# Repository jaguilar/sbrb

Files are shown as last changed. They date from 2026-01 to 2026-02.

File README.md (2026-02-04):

# SBRB -- Another Arduino-based Self-Balancing Robot

## Overview

Well, is it really Arduino based? A little bit, but it's a funky
hybrid of ESP-IDF and Arduino code. This bot can be controlled
using a BLE gamepad like the Steam Controller (BLE firmware).

## Features

- Remote controllable
- Self-balancing
- Telemetry and bluetooth-based tuning
- Battery monitoring (assumes 2S LiPo, see schematics for voltage divider
  requirements)

## Schematics

There is a sort-of-working KiCad schematic in the `kicad` directory.
This is not actually what I used: I soldered together a protoboard.
Also, the pin configuration on the proto board and in the code is
significantly altered from what is shown in the schematic.

## Building

The bot uses 3D printed parts from this [OnShape document](https://cad.onshape.com/documents/8def695b0fbd504a5c261cca/w/9027d04ea9ab3dbc2eeb5165/e/62757f7892dd92c4c3207e76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).

## BOM

In addition to the 3D printed parts, you need:

* 2x 693ZZ bearings
* 2x 500 RPM N20 motors with gearboxes (I used [these](https://www.aliexpress.us/item/3256807135186419.html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))
* 2x TT motor wheels
* 1x 50x70mm perfboard
* 1x MPU-6050 breakout board
* 1x ESP32-S3 Zero Dev board
* 1x Mini360 buck converter
* 1x 20k resistor (buy a 0508 assortment of SMD parts, should have the caps and diode too)
* 1x 10k resistor
* 2x 100nF capacitor SMD 
* 1x 470uF capacitor throughhole (buy an assortment)
* 1x 100uF capacitor throughhole
* 1x 1N5819 Schottky diode
* 1x 3A fuse (you can use less, 2A would be fine)
* 1x throughhole switch capable of supporting same amperage as your
  fuse, or a lesser amperage and a MOSFET capable of supporting that current
* 1x TB6612FNG motor driver breakout board
* 1x 2S LiPo battery
* 3x JST-XH 2 pin through hole header
* 2x JST-XH 4 pin through hole header
* JST-XH female connectors for wires
* Various M2 and M3 hex head screws and nuts
* Various 24 AWG hookup wire
* XT30 connectors for battery

## Media



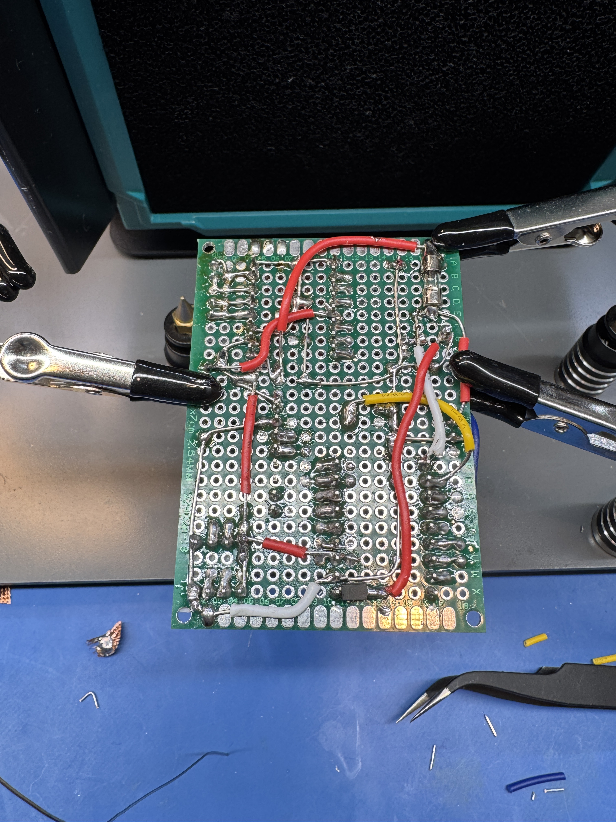
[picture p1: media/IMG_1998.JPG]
Perfboard picture 1


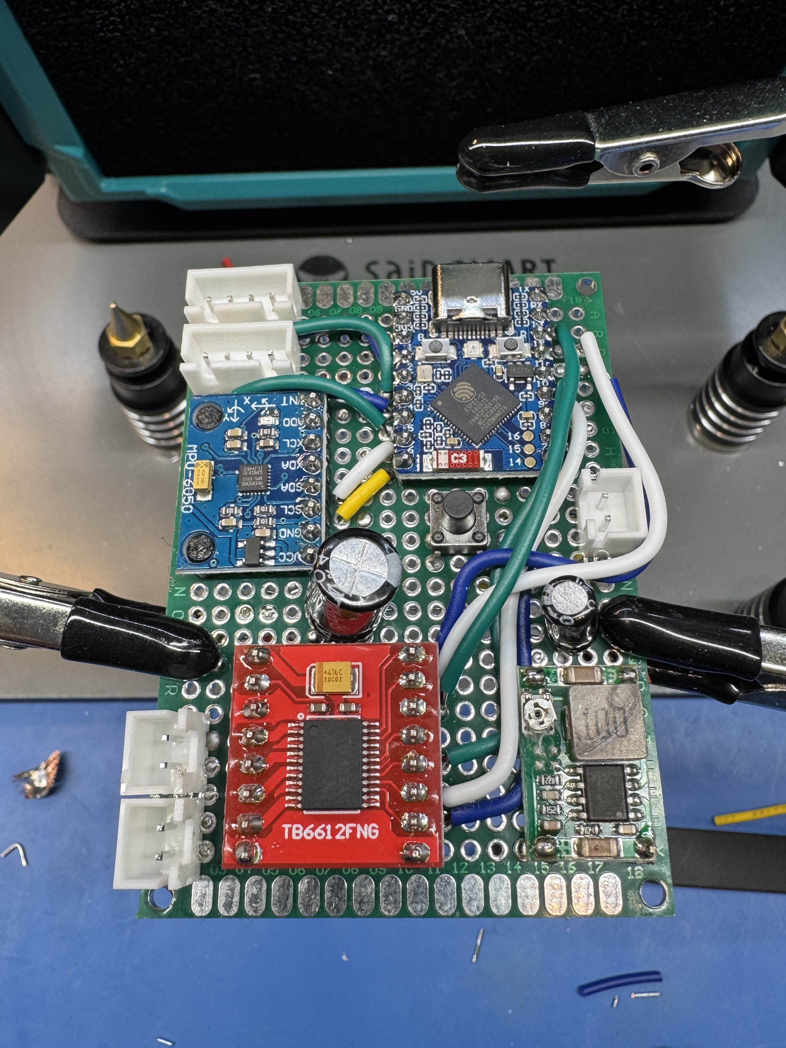
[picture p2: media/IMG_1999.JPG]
Perfboard picture 2


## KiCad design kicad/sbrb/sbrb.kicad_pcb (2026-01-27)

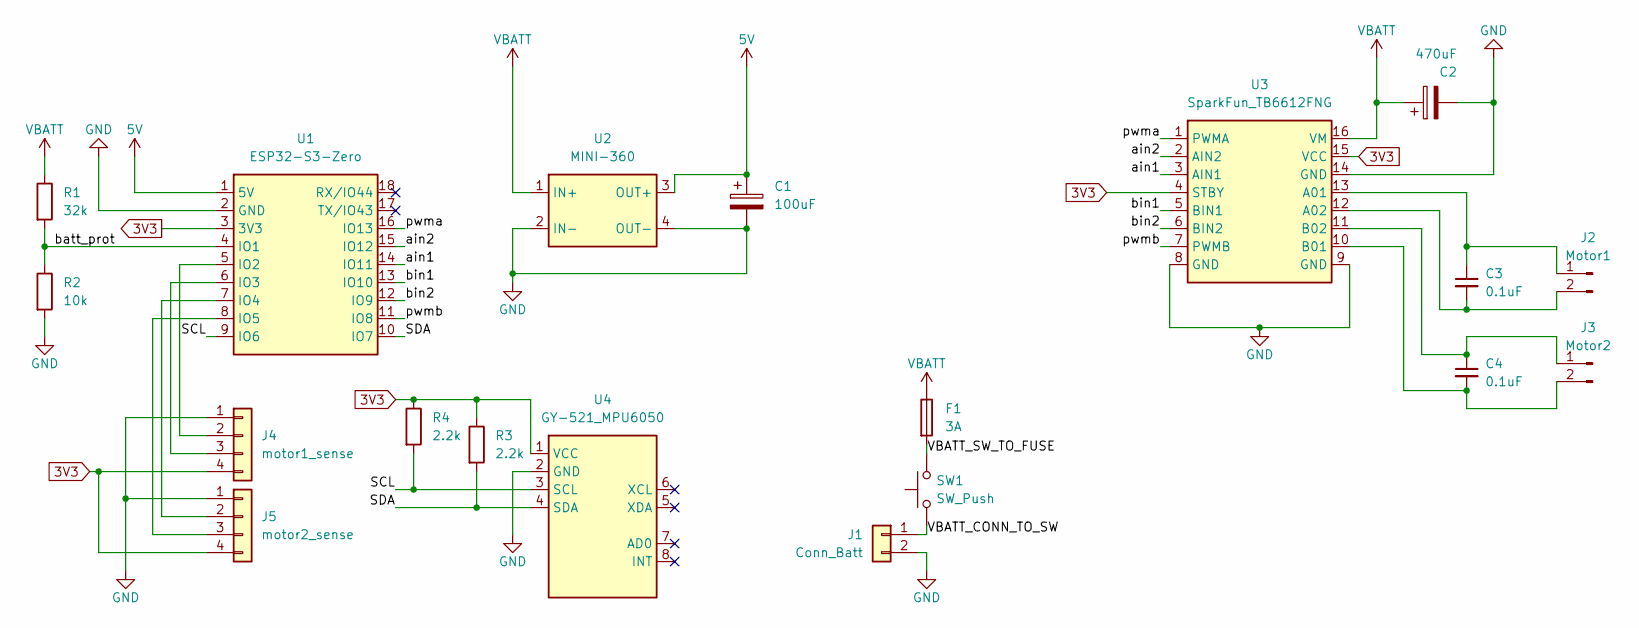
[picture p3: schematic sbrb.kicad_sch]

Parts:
C1: 100uF; CP_Radial_D6.3mm_P2.50mm
C2: 470uF; CP_Radial_D8.0mm_P3.80mm
C3, C4: 0.1uF; C_0805_2012Metric
F1: 3A; Fuse_Schurter_UMT250
J1: Conn_Batt; JST_XH_B2B-XH-AM_1x02_P2.50mm_Vertical
J2: Motor1; JST_XH_B2B-XH-AM_1x02_P2.50mm_Vertical
J3: Motor2; JST_XH_B2B-XH-AM_1x02_P2.50mm_Vertical
J4: motor1_sense; JST_XH_B4B-XH-AM_1x04_P2.50mm_Vertical
J5: motor2_sense; JST_XH_B4B-XH-AM_1x04_P2.50mm_Vertical
R1: 32k; R_0805_2012Metric
R2: 10k; R_0805_2012Metric
R3, R4: 2.2k; R_0805_2012Metric
SW1: SW_Push; SW_SPST_FSMSM
U1: ESP32-S3-Zero; ESP32-S3-Zero_Breakout
U2: MINI-360; mini360
U3: SparkFun_TB6612FNG; TB6612FNG_Breakout
U4: GY-521_MPU6050; GY-521

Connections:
3V3: J4.4, J5.4, R3.1, R4.1, U1.3 (3V3), U3.4 (STBY), U3.15 (VCC), U4.1 (VCC)
5V: C1.1, U1.1 (5V), U2.3 (OUT+)
/SCL: R4.2, U1.9 (IO6), U4.3 (SCL)
/SDA: R3.2, U1.10 (IO7), U4.4 (SDA)
/VBATT_CONN_TO_SW: J1.1, SW1.1
/VBATT_SW_TO_FUSE: F1.2, SW1.2
/ain1: U1.14 (IO11), U3.3 (AIN1)
/ain2: U1.15 (IO12), U3.2 (AIN2)
/batt_prot: R1.2, R2.1, U1.4 (IO1)
/bin1: U1.13 (IO10), U3.5 (BIN1)
/bin2: U1.12 (IO9), U3.6 (BIN2)
/pwma: U1.16 (IO13), U3.1 (PWMA)
/pwmb: U1.11 (IO8), U3.7 (PWMB)
GND: C1.2, C2.2, J1.2, J4.1, J5.1, R2.2, U1.2 (GND), U2.2 (IN-), U2.4 (OUT-), U3.8 (GND), U3.9 (GND), U3.14 (GND), U4.2 (GND)
unnamed: C3.1, J2.1, U3.13 (A01)
unnamed: C3.2, J2.2, U3.12 (A02)
unnamed: C4.1, J3.1, U3.11 (B02)
unnamed: C4.2, J3.2, U3.10 (B01)
unnamed: J4.2, U1.5 (IO2)
unnamed: J4.3, U1.6 (IO3)
unnamed: J5.2, U1.7 (IO4)
unnamed: J5.3, U1.8 (IO5)
VBATT: C2.1, F1.1, R1.1, U2.1 (IN+), U3.16 (VM)

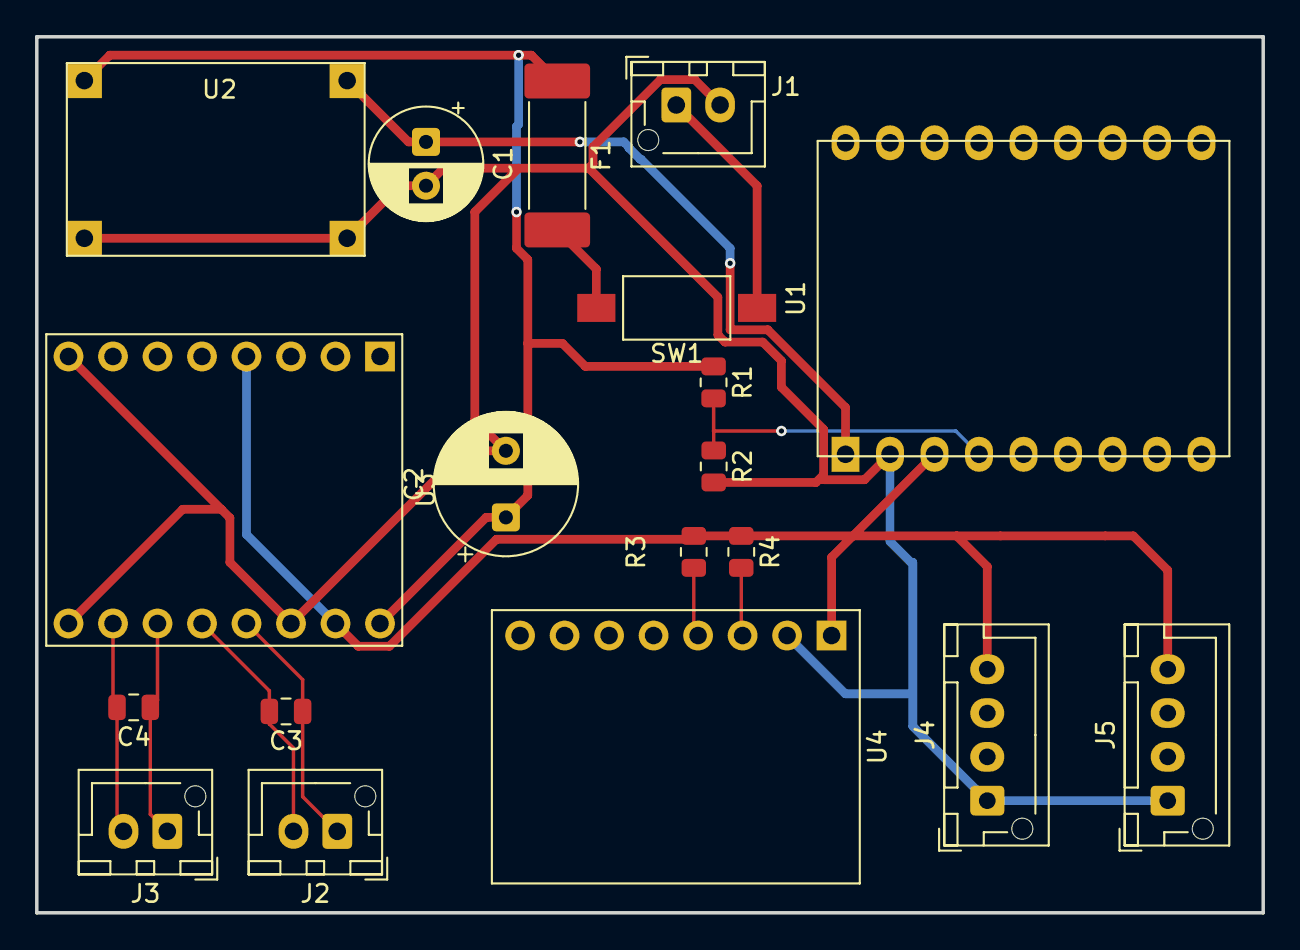
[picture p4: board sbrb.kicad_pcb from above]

Board: 4 copper layers, 70.0 x 50.0 mm, 19 parts (0 on the bottom side), 23 nets.

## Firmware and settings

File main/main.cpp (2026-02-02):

#include <Arduino.h>
#include <ESPmDNS.h>
#include <freertos/FreeRTOS.h>
#include <freertos/task.h>
#include <stdio.h>
#include <sys/unistd.h>

#include <cmath>
#include <cstdint>
#include <cstdio>
#include <cstdlib>
#include <cstring>
#include <functional>
#include <limits>
#include <memory>
#include <string_view>

#include "Adafruit_NeoPixel.h"
#include "FreeRTOSConfig.h"
#include "IPAddress.h"
#include "MPU6050.h"
#include "PIDController.h"
#include "ServoMotor.h"
#include "WiFi.h"
#include "WiFiUdp.h"
#include "Wire.h"
#include "driver/gpio.h"
#include "driver/rtc_io.h"
#include "esp32-hal-adc.h"
#include "esp32-hal-gpio.h"
#include "esp32-hal-log.h"
#include "esp32-hal.h"
#include "esp_err.h"
#include "esp_log.h"
#include "esp_sleep.h"
#include "esp_timer.h"
#include "freertos/idf_additions.h"
#include "freertos/task.h"
#include "pins_arduino.h"
#include "portmacro.h"
#include "soc/gpio_num.h"
#include "uni_property.h"

#ifdef CONFIG_BT_MODE_TUNE
#include <charconv>
#include <format>
#include <string>
#include <system_error>

#include "NimBLEAdvertising.h"
#include "NimBLEAttValue.h"
#include "NimBLEDevice.h"
#endif
#ifdef CONFIG_BT_MODE_PAD
#include <btstack_port_esp32.h>
#include <btstack_run_loop.h>
#include <gap.h>
#include <uni.h>
#endif

#define TAG "SBRB"

namespace sbrb {

constexpr int kMPU6050SDA = 5;
constexpr int kMPU6050SCL = 6;
constexpr int kBattVoltagePin = 7;
constexpr int kSleepPin = 8;

constexpr int kMotorLPwmPin = 12;
constexpr int kMotorLFwdPin = RX;
constexpr int kMotorLRevPin = 13;
constexpr int kMotorLPulsePin = 2;
constexpr int kMotorLControlPin = 1;

constexpr int kMotorRPwmPin = 9;
constexpr int kMotorRFwdPin = 11;
constexpr int kMotorRRevPin = 10;
constexpr int kMotorRPulsePin = 3;
constexpr int kMotorRControlPin = 4;

constexpr int kNeoPixelPin = 21;
constexpr int kNeoPixelCount = 1;
static Adafruit_NeoPixel neo_pixel(kNeoPixelCount, kNeoPixelPin,
                                   NEO_RGB + NEO_KHZ800);

constexpr float kBattVoltageScale = 3.3f;
constexpr float kDividerRatio = 1.0f / 3.0f;

std::unique_ptr<ServoMotor> motor_l;
std::unique_ptr<ServoMotor> motor_r;
std::unique_ptr<MPU6050> mpu;

struct State {
  int64_t now = millis();
  int loop_iter = 0;

  int last_steering_iter = 0;
  uint32_t now_us = micros();
  float dt = 0;  // The change in time (s) since the last sample.

  float pitch = -90;  // Degrees, negative if we're tilted forward.
  float pitch_rate =
      0;  // Rate in the change of pitch (i.e. the raw gyro reading.)

  float yaw_rate = 0;     // Degrees/s, smoothed via EWMA.
  float wheel_speed = 0;  // Degrees/s, averaged between the two motors,
                          // smoothed via EWMA.
  float accel = 0;        // Degrees/s^2, smoothed via EWMA.

  float wheel_speed_left = 0;
  float wheel_speed_right = 0;

  int64_t last_time_standing = now - 1000;
  bool fallen() const { return now - last_time_standing > 250; }

  // Command state, useful for debugging.
  float commanded_yaw_rate;
  float commanded_speed;
  float commanded_pitch;
  float commanded_duty_left;
  float commanded_duty_right;

  // The "now_us" time of the sample that was last used to compute the balance
  // and steering commands. Used to compute dt for the PID controller update
  // loops.
  uint32_t last_balance_cmd_us = 0;
  uint32_t last_steering_cmd_us = 0;
};

// The controller for the robot. Contains the PID controllers for the robot.
struct Controller {
  // The pitch controller takes in the current pitch and the desired pitch and
  // emits motor average duty cycle to achieve that pitch. Basic tuning
  // intuition is if we're pitched forward of where we want to be, we should be
  // running the motors *toward* the direction we're pitched. Running the motors
  // in one direction tends to push the wheels in the opposite direction,
  // gain will be positive.
  PIDController pitch_controller{PIDController::Params{
      .kp = 30.f,
      .ti = 0.6f,
      .td = 0.035f,
      .output_range = {{-255, 255}},
  }};

  // Controls the speed of the wheels by adjusting the target pitch angle.
  // The gain on this controller is quite low, because the wheel speed is in
  // degrees per second. The idea here is that the desired pitch might be
  // only a couple of degrees forward when we want to go 720 degrees per second.
  //
  // The gain's sign is set this way: if we want to go forward, we need to pitch
  // forward. To pitch forward, we need to the pitch to be negative.
  PIDController wheel_speed_controller{{
      .kp = -0.005f,
      .ti = 2.5f,
      .td = 0.01f,
      .output_range = {{-20, 20}},
  }};

  // Controls the differential drive that controls the yaw rate. (I.e. for each
  // degree per second of yaw rate error, how much duty cycle should we add to
  // the left motor and subtract from the right motor?)
  //
  // As a reminder to myself, in robotics, clockwise rotation about Z is
  // negative. Error is setpoint - measurement. So, let's suppose setpoint is
  // zero, and I observe that I'm turning to the right (measurement is
  // negative). That will make my error positive. When my error is positive, I
  // need to turn left to compensate, which is to say that I need to add duty to
  // the right motor and subtract from the left. So the output of this is the
  // differential duty cycle to add to the right motor and subtract from the
  // left.
  PIDController yaw_rate_controller{PIDController::Params{
      .kp = 0.25f, .ti = 0.0, .td = 0.0f, .output_range = {{-50, 50}}}};

  int32_t axis_y = 0;  // Used to compute setpoints.
  int32_t axis_rx = 0;
};
Controller pid_controllers;

static volatile bool sleep_soon = false;
void IRAM_ATTR SleepPinISR() { sleep_soon = true; }

[[noreturn]] void GoToSleep() {
  motor_l->DeepSleepPrepare();
  motor_r->DeepSleepPrepare();

  neo_pixel.clear();
  neo_pixel.show();

  const auto pin = static_cast<gpio_num_t>(kSleepPin);
  pinMode(pin, INPUT_PULLUP);
  do {
    delay(100);  // Debounce, the sleep button.
  } while (!digitalRead(pin));
  delay(25);

  // We need to respect all holds, particularly on the motor pins,
  // while we are asleep.
  gpio_deep_sleep_hold_en();

  rtc_gpio_init(pin);
  rtc_gpio_pullup_en(pin);
  esp_sleep_enable_ext0_wakeup(pin, 0);
  esp_deep_sleep_start();
}

void WakeUp() {
  rtc_gpio_deinit(static_cast<gpio_num_t>(kSleepPin));
  motor_l->DeepSleepResume();
  motor_r->DeepSleepResume();

  // Don't finish waking up until the sleep button is released.
  pinMode(kSleepPin, INPUT_PULLUP);
  while (!digitalRead(kSleepPin)) {
    delay(100);
  }
  delay(50);
}

static void InitTuningService();

// The battery is connected to kBattVoltagePin via a voltage divider.
// The divider is 20k/10k. This means we'll see a voltage which is roughly
// 2/3rds of the actual battery voltage.
int BatteryMillivolts() {
  constexpr int kMillivoltsScale = 16 / kDividerRatio;
  const int batt_milivolts =
      (analogReadMilliVolts(kBattVoltagePin) * kMillivoltsScale) / 16;
  return batt_milivolts;
}

static int smoothed_battery_millivolts = -1000;
void MonitorBattery(void*) {
  constexpr float kAlpha = 0.05;
  if (smoothed_battery_millivolts < -100) {
    smoothed_battery_millivolts = BatteryMillivolts();
  } else {
    smoothed_battery_millivolts = (smoothed_battery_millivolts * (1 - kAlpha) +
                                   BatteryMillivolts() * kAlpha);
  }
}

#if CONFIG_TELEMETRY_ENABLED
struct TelemetryData {
  uint32_t now_ms;
  float yaw_rate;
  float yaw_p;
  float yaw_i;
  float yaw_d;
  float yaw_err;
  float yaw_cmd;
  float motor_l_duty;
  float motor_r_duty;
  float pitch;
};

static portMUX_TYPE telemetry_state_mu = portMUX_INITIALIZER_UNLOCKED;
static TelemetryData telemetry_state;
static IPAddress telemetry_addr;
static constexpr int kTeleplotPort = 47269;
static WiFiUDP udp;

void QueueTelemetry(const TelemetryData& d) {
  if (portTRY_ENTER_CRITICAL(&telemetry_state_mu, 0)) {
    telemetry_state = d;
    portEXIT_CRITICAL(&telemetry_state_mu);
  }
}

void SendTelemetry(void*) {
  static uint32_t last_send = 0;
  if (!portTRY_ENTER_CRITICAL(&telemetry_state_mu, 0)) {
    ESP_LOGW("SBRB", "Failed to enter critical section for telemetry");
    return;
  }
  TelemetryData state = telemetry_state;
  IPAddress addr = telemetry_addr;
  portEXIT_CRITICAL(&telemetry_state_mu);
  if (addr == IPAddress()) {
    ESP_LOGW("SBRB", "Telemetry address not resolved");
    return;
  }
  if (state.now_ms == last_send) {
    ESP_LOGW("SBRB", "Telemetry not updated");
    return;
  }
  last_send = state.now_ms;

  // Assemble a UDP packet containing the telemetry. For the sake of argument we
  // will assume no more than one packet is needed, but this is a hack.
  char packet_buf[1432];
  int packet_len = 0;

  auto add_field = [&](std::string_view name, float value) {
    int written = snprintf(&packet_buf[packet_len],
                           sizeof(packet_buf) - packet_len, "%*s:%lu:%.4f\n",
                           name.size(), name.data(), state.now_ms, value);
    if (written < 0 || written >= sizeof(packet_buf) - packet_len) {
      packet_buf[packet_len] = 0;
    }
    packet_len += written;
  };

  add_field("dyaw", state.yaw_rate);
  add_field("yaw_p", state.yaw_p);
  add_field("yaw_i", state.yaw_i);
  add_field("yaw_d", state.yaw_d);
  add_field("yaw_err", state.yaw_err);
  add_field("yaw_cmd", state.yaw_cmd);
  add_field("motor_l_duty", state.motor_l_duty);
  add_field("motor_r_duty", state.motor_r_duty);
  add_field("pitch", state.pitch);

  udp.beginPacket(addr, kTeleplotPort);
  udp.write(reinterpret_cast<const uint8_t*>(packet_buf), packet_len);
  if (udp.endPacket() < 0) {
    ESP_LOGD("SBRB", "Failed to send telemetry packet of length %d",
             packet_len);
  } else {
    ESP_LOGD("SBRB", "Sent telemetry packet of length %d", packet_len);
  }
}

TelemetryData MakeTelemetryPacket(const State& state,
                                  const Controller& controller) {
  TelemetryData packet;
  packet.now_ms = state.now;
  packet.yaw_rate = state.yaw_rate;
  packet.yaw_p = controller.yaw_rate_controller.p();
  packet.yaw_i = controller.yaw_rate_controller.i();
  packet.yaw_d = controller.yaw_rate_controller.d();
  packet.yaw_err = controller.yaw_rate_controller.error();
  packet.yaw_cmd = state.commanded_yaw_rate;
  packet.motor_l_duty = state.commanded_duty_left;
  packet.motor_r_duty = state.commanded_duty_right;
  packet.pitch = state.pitch;
  return packet;
}

#endif

void LowPriorityTasks(void*) {
  struct {
    void (*work)(void*);
    uint32_t period;
    uint32_t last_done = millis() - period;
    bool IsExpired() const { return millis() - last_done > period; }
    void MarkDone() { last_done = millis(); }
    uint32_t SleepDuration() const {
      const uint32_t since_done = millis() - last_done;
      if (since_done > period) {
        return 0;
      }
      return period - since_done;
    }
  } jobs[] = {
      {.work = MonitorBattery, .period = 1000},
#if CONFIG_TELEMETRY_ENABLED
      {.work = SendTelemetry, .period = 50},
#endif
  };

  while (true) {
    uint32_t sleep_time = std::numeric_limits<uint32_t>::max();
    for (auto& job : jobs) {
      if (job.IsExpired()) {
        job.work(nullptr);
        job.MarkDone();
      }
      sleep_time = std::min(sleep_time, job.SleepDuration());
    }
    if (sleep_time > 50) {
      ESP_LOGW(TAG, "Sleep duration %d too long", sleep_time);
      sleep_time = 50;
    }
    vTaskDelay(pdMS_TO_TICKS(sleep_time));
  }
}

constexpr int kBalanceFreq = 500;
constexpr int kSteeringFreq = 20;
constexpr int kSteerOncePerIters = kBalanceFreq / kSteeringFreq;

void UpdateState(State& state, bool log_details = false) {
  state.now = millis();
  state.loop_iter++;
  auto now_us = micros();
  state.dt = (now_us - state.now_us) / 1000000.0f;
  state.now_us = now_us;

  if (state.dt < 0.0005f) {
    // Not enough time has passed since the last sample. Skip this iteration.
    return;
  }

  constexpr float kAlpha = 0.98f;
  constexpr float kRadToDeg = 180.0f / 3.14159265f;

  // MPU6050 Defaults
  constexpr float kAccelScale = 16384.0f;
  constexpr float kGyroScale = 32.8f;
  int16_t ax_raw, ay_raw, az_raw, gx_raw, gy_raw, gz_raw;
  mpu->getMotion6(&ax_raw, &ay_raw, &az_raw, &gx_raw, &gy_raw, &gz_raw);

  // Convert to physical units
  const float ax = ax_raw / kAccelScale;
  const float ay = ay_raw / kAccelScale;
  const float az = az_raw / kAccelScale;
  const float gy = gy_raw / kGyroScale;
  const float gz = gz_raw / kGyroScale;

  float acc_angle_y = atan2(-ax, sqrt(ay * ay + az * az)) * kRadToDeg;
  state.pitch =
      (state.pitch + gy * state.dt) * kAlpha + (1.0f - kAlpha) * acc_angle_y;

  // Update pitch and yaw rates. Tuned for a cutoff frequency of ~4Hz.
  constexpr auto kGyroAlpha = 0.05f;
  constexpr auto kGryoAlphaInv = 1.0f - kGyroAlpha;
  state.pitch_rate = kGyroAlpha * gy + kGryoAlphaInv * state.pitch_rate;
  state.yaw_rate = kGyroAlpha * gz + kGryoAlphaInv * state.yaw_rate;

  state.wheel_speed_left = motor_l->GetSpeed();
  state.wheel_speed_right = motor_r->GetSpeed();
  const float avg_speed =
      (state.wheel_speed_left + state.wheel_speed_right) / 2.0f;
  // Wheel speed is filtered less aggressively than the gyro since we expect
  // a higher frequency of real wheel speed changes.
  constexpr auto kSpeedAlpha = 0.1f;
  const float raw_accel = (avg_speed - state.wheel_speed) / state.dt;
  state.accel = kSpeedAlpha * raw_accel + (1.0f - kSpeedAlpha) * state.accel;
  state.wheel_speed =
      kSpeedAlpha * avg_speed + (1.0f - kSpeedAlpha) * state.wheel_speed;

  const float abspitch = std::abs(state.pitch);
  if (state.fallen() && abspitch <= 3) {
    state.last_time_standing = state.now;
  } else if (abspitch <= 30) {
    state.last_time_standing = state.now;
  }
}

void Control(State& state, Controller& control) {
  // Compute the setpoints for desired turn rate and forward and reverse.
  constexpr float kSpeedRange = 920.0f;  // 120 RPM is max commanded speed.
  constexpr float kYawRange =
      180.0f;  // 90 degrees per second is max turn rate.
  constexpr float kSpeedSaturation =
      512.0f;  // Once the y-axis reaches +-512, the output will be saturated.
  constexpr float kYawSaturation =
      450.0f;  // Once the rx-axis reaches +-450, the output will be saturated.

  // axis_y+ is backward, but speed+ is forward, so we negate the axis.
  const float speed_setpoint =
      std::clamp(-control.axis_y * kSpeedRange / kSpeedSaturation, -kSpeedRange,
                 kSpeedRange);
  // axis_rx+ is clockwise rotation, but yaw rate is negative for clockwise.
  const float yaw_setpoint = std::clamp(
      -control.axis_rx * kYawRange / kYawSaturation, -kYawRange, kYawRange);

  if (state.loop_iter - state.last_steering_iter >= kSteerOncePerIters) {
    state.last_steering_iter = state.loop_iter;
    // Try to find a pitch that will get us to the desired speed.
    const float dt = (state.now_us - state.last_steering_cmd_us) / 1000000.0f;
    state.commanded_pitch = control.wheel_speed_controller.Compute(
        speed_setpoint, state.wheel_speed, state.accel, dt);
    state.last_steering_cmd_us = state.now_us;
  }

  // Try to find a duty cycle that will get us to the desired pitch.
  const float dt = (state.now_us - state.last_balance_cmd_us) / 1000000.0f;
  float duty = control.pitch_controller.Compute(
      state.commanded_pitch, state.pitch, state.pitch_rate, dt);
  float yaw_duty =
      control.yaw_rate_controller.Compute(yaw_setpoint, state.yaw_rate, dt);
  state.last_balance_cmd_us = state.now_us;

  // Scale the duty cycle based on the battery voltage.
  // We did the initial robot tuning at 7V on a bench power supply.
  // If the battery voltage is higher than that we need to command
  // a lower duty cycle to compensate. This does also mean we'll never
  // run the motor at full power when the battery is fully charged,
  // but that's okay because doing it this way means we'll give a
  // consistent experience no matter the charge level. Note that there
  // is no need for clamping here as the robot will shut off if the
  // power is substantially lower than the tuning voltage to protect
  // the battery.
  constexpr float kTuningVbattMV = 7000;
  if (smoothed_battery_millivolts > 6000) {
    // Don't bother with this step if we're not connected to motor power.
    duty *= kTuningVbattMV / smoothed_battery_millivolts;
    yaw_duty *= kTuningVbattMV / smoothed_battery_millivolts;
  }

  state.commanded_duty_left = duty - yaw_duty;
  state.commanded_duty_right = duty + yaw_duty;
  motor_l->SetDuty(state.commanded_duty_left);
  motor_r->SetDuty(state.commanded_duty_right);
}

void SetPixelColor(float pitch) {
  constexpr float kRedPitch = 10.0f;

  const float lerp = std::min(1.0f, std::abs(pitch) / kRedPitch);
  neo_pixel.setPixelColor(0, lerp * 255, (1.0f - lerp) * 255, 0);
  neo_pixel.show();
}

#if CONFIG_BT_MODE_TUNE

char cmd_buf[100];
int cmd_idx = 0;

void DoTuningCommand(std::string_view cmd) {
  while (true) {
    // Strip leading whitespace
    while (!cmd.empty() && std::isspace(cmd.front())) {
      cmd.remove_prefix(1);
    }
    if (cmd.empty()) break;

    // Find the end of the command string (first whitespace)
    size_t cmd_end = 0;
    while (cmd_end < cmd.size() && !std::isspace(cmd[cmd_end])) {
      cmd_end++;
    }

    std::string_view command = cmd.substr(0, cmd_end);
    cmd.remove_prefix(cmd_end);

    // Strip whitespace before value
    while (!cmd.empty() && std::isspace(cmd.front())) {
      cmd.remove_prefix(1);
    }

    if (cmd.empty()) {
      log_e("Command %.*s missing value", static_cast<int>(command.size()),
            command.data());
      break;
    }

    float value;
    auto result = std::from_chars(cmd.data(), cmd.data() + cmd.size(), value);
    if (result.ec == std::errc()) {
      cmd.remove_prefix(result.ptr - cmd.data());

      if (command == "pp") {
        pid_controllers.pitch_controller.set_kp(value);
        ESP_LOGI(TAG, "Pitch: Set kp to %f", value);
      } else if (command == "pi") {
        pid_controllers.pitch_controller.set_ti(value);
        ESP_LOGI(TAG, "Pitch: Set ti to %f", value);
      } else if (command == "pd") {
        pid_controllers.pitch_controller.set_td(value);
        ESP_LOGI(TAG, "Pitch: Set td to %f", value);
      } else if (command == "wp") {
        pid_controllers.wheel_speed_controller.set_kp(value);
        ESP_LOGI(TAG, "Wheel: Set kp to %f", value);
      } else if (command == "wi") {
        pid_controllers.wheel_speed_controller.set_ti(value);
        ESP_LOGI(TAG, "Wheel: Set ti to %f", value);
      } else if (command == "wd") {
        pid_controllers.wheel_speed_controller.set_td(value);
        ESP_LOGI(TAG, "Wheel: Set td to %f", value);
      } else if (command == "db") {
        motor_l->set_deadband(static_cast<int>(value));
        motor_r->set_deadband(static_cast<int>(value));
        ESP_LOGI(TAG, "Set deadband to %d", static_cast<int>(value));
      } else {
        log_e("Unknown command: %.*s", static_cast<int>(command.size()),
              command.data());
      }
    } else {
      log_e("Failed to parse value for command %.*s",
            static_cast<int>(command.size()), command.data());
      // Consume the bad token
      while (!cmd.empty() && !std::isspace(cmd.front())) {
        cmd.remove_prefix(1);
      }
    }
  }
}

void MaybeReadCommand() {
  if (!Serial.available()) return;
  int c;
  while (cmd_idx < sizeof(cmd_buf) - 1 &&
         (cmd_idx == 0 || cmd_buf[cmd_idx - 1] != '\n') &&
         (c = Serial.read()) != -1) {
    cmd_buf[cmd_idx++] = c;
    ESP_LOGI(TAG, "Received char: %c", c);
  }

  std::string_view cmd_view(cmd_buf, cmd_idx);
  if (!cmd_view.empty() &&
      (cmd_view.back() == '\n' || cmd_view.back() == '\r')) {
    DoTuningCommand(cmd_view);
    std::memset(cmd_buf, 0, sizeof(cmd_buf));
    cmd_idx = 0;
  }
}
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
void loop() {
  using namespace sbrb;
  static State state;
  static int print_counter = 0;
  bool print_details = false;
  if (print_details) print_counter = 0;

  static auto last_loop_start = micros();
  const auto wait_start = micros();
  auto interloop_time = wait_start - last_loop_start;
  last_loop_start = wait_start;

  xTaskNotifyWait(0, 1, nullptr, portMAX_DELAY);
  const auto loop_start = micros();
  UpdateState(state, print_details);

  // Do shutdown checks first and foremost.
  if (smoothed_battery_millivolts < 6800 || sleep_soon) {
    // GoToSleep();
  }

  SetPixelColor(state.pitch);

  if (state.fallen()) {
    motor_l->SetDuty(0);
    motor_r->SetDuty(0);
    pid_controllers.pitch_controller.Reset();
    pid_controllers.wheel_speed_controller.Reset();
    pid_controllers.yaw_rate_controller.Reset();
  } else {
    Control(state, pid_controllers);
  }

#if CONFIG_TELEMETRY_ENABLED
  static int32_t last_telemetry = state.now;
  if (state.now - last_telemetry > 50) {
    last_telemetry = state.now;
    TelemetryData packet = MakeTelemetryPacket(state, pid_controllers);
    QueueTelemetry(packet);
  }
#endif

  const auto loop_end = micros();
  static int last_loop_log = millis();
  if (millis() - last_loop_log > 1000 && !print_details && print_counter != 0) {
    // Check for violated loop timing expectations.
    if (interloop_time > 2500) {
      ESP_LOGE(TAG, "Interloop time was %d usec",
               static_cast<int>(interloop_time));
    } else if (loop_end - loop_start > 1500) {
      ESP_LOGE(TAG, "Control loop took %d usec",
               static_cast<int>(loop_end - loop_start));
    } else {
      return;  // We didn't print anything.
    }
    last_loop_log = millis();
  }
}

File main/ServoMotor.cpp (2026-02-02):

#include "ServoMotor.h"

#include <Arduino.h>

#include <algorithm>
#include <cstdint>
#include <memory>
#include <utility>

#include "driver/gpio.h"
#include "driver/pulse_cnt.h"
#include "esp_check.h"
#include "esp_err.h"
#include "freertos/idf_additions.h"
#include "portmacro.h"
#include "freertos/semphr.h"
#include "soc/gpio_num.h"

// Define LOG_TAG if not already defined for ESP logging macros
#ifndef LOG_TAG
#define LOG_TAG "ServoMotor"
#endif

ServoMotor::ServoMotor(pcnt_unit_handle_t unit, pcnt_channel_handle_t chan_a,
                       pcnt_channel_handle_t chan_b, int pwm_pin, int fwd_pin,
                       int rev_pin, int deadband)
    : unit_(unit),
      chan_a_(chan_a),
      chan_b_(chan_b),
      pwm_pin_(pwm_pin),
      fwd_pin_(fwd_pin),
      rev_pin_(rev_pin),
      deadband_(deadband),
      pid_(PIDController::Params{
          .kp = .5f,
          .ti = 0.05f,
          .td = 0.01f,
          .output_range = std::make_pair(-255.0f, 255.0f)}) {}

ServoMotor::~ServoMotor() {
  // Clean up PCNT resources if needed.
  // Note: PCNT resource lifecycle management might be needed here depending on
  // if we want to support destruction. For now, assuming static lifetime or
  // user handles it. Ideally: disable, del_channel, del_unit. But since this is
  // a refactor of static setup, simple is fine.
}

std::unique_ptr<ServoMotor> ServoMotor::Create(const Config& config) {
  pcnt_unit_handle_t pcnt_unit = NULL;
  pcnt_unit_config_t cfg = {
      .low_limit = -32768,
      .high_limit = 32767,
      .flags =
          {
              .accum_count = true,
          },
  };
  // Using ESP_ERROR_CHECK usually aborts. For a factory, maybe we should return
  // nullptr on failure? But original code used ESP_ERROR_CHECK, so we stick to
  // that or let it crash on failure. To allow graceful failure, we could check
  // return codes. Sticking to original behavior:
  ESP_ERROR_CHECK(pcnt_new_unit(&cfg, &pcnt_unit));

  pcnt_glitch_filter_config_t filter_cfg = {
      .max_glitch_ns = 1000,
  };
  ESP_ERROR_CHECK(pcnt_unit_set_glitch_filter(pcnt_unit, &filter_cfg));

  pcnt_chan_config_t chan_a_cfg = {
      .edge_gpio_num = config.pulse_pin,
      .level_gpio_num = config.control_pin,
  };
  pcnt_channel_handle_t chan_a;
  ESP_ERROR_CHECK(pcnt_new_channel(pcnt_unit, &chan_a_cfg, &chan_a));

  pcnt_chan_config_t chan_b_cfg = {
      .edge_gpio_num = config.control_pin,
      .level_gpio_num = config.pulse_pin,
  };
  pcnt_channel_handle_t chan_b;
  ESP_ERROR_CHECK(pcnt_new_channel(pcnt_unit, &chan_b_cfg, &chan_b));

  ESP_ERROR_CHECK(
      pcnt_channel_set_edge_action(chan_a, PCNT_CHANNEL_EDGE_ACTION_INCREASE,
                                   PCNT_CHANNEL_EDGE_ACTION_DECREASE));
  ESP_ERROR_CHECK(
      pcnt_channel_set_level_action(chan_a, PCNT_CHANNEL_LEVEL_ACTION_KEEP,
                                    PCNT_CHANNEL_LEVEL_ACTION_INVERSE));

  ESP_ERROR_CHECK(
      pcnt_channel_set_edge_action(chan_b, PCNT_CHANNEL_EDGE_ACTION_DECREASE,
                                   PCNT_CHANNEL_EDGE_ACTION_INCREASE));
  ESP_ERROR_CHECK(
      pcnt_channel_set_level_action(chan_b, PCNT_CHANNEL_LEVEL_ACTION_KEEP,
                                    PCNT_CHANNEL_LEVEL_ACTION_INVERSE));

  ESP_ERROR_CHECK(pcnt_unit_add_watch_point(pcnt_unit, cfg.high_limit));
  ESP_ERROR_CHECK(pcnt_unit_add_watch_point(pcnt_unit, cfg.low_limit));

  ESP_ERROR_CHECK(pcnt_unit_enable(pcnt_unit));
  ESP_ERROR_CHECK(pcnt_unit_start(pcnt_unit));

  // Initialize Motor Pins
  pinMode(config.pwm_pin, OUTPUT);
  pinMode(config.rev_pin, OUTPUT);
  pinMode(config.fwd_pin, OUTPUT);
  digitalWrite(config.rev_pin, LOW);
  digitalWrite(config.fwd_pin, LOW);
  analogWriteFrequency(config.pwm_pin, 20000);
  analogWriteResolution(config.pwm_pin, 8);
  analogWrite(config.pwm_pin, 0);

  auto servo_motor =
      new ServoMotor(pcnt_unit, chan_a, chan_b, config.pwm_pin, config.fwd_pin,
                     config.rev_pin, config.deadband);

  xTaskCreate(
      +[](void* arg) { reinterpret_cast<ServoMotor*>(arg)->Update(); },
      "ServoMotor", 4098, servo_motor, 0, &servo_motor->task_);

  return std::unique_ptr<ServoMotor>(servo_motor);
}

void ServoMotor::DeepSleepPrepare() {
  vTaskSuspend(task_);
  OutputDuty(0);
  gpio_hold_en(static_cast<gpio_num_t>(fwd_pin_));
  gpio_hold_en(static_cast<gpio_num_t>(rev_pin_));
}

void ServoMotor::DeepSleepResume() {
  // Note that when we resume from deep sleep we do not need to resume
  // the task_ or set the duty. Those values are lost to us since the
  // memory went away. But what we do need to do is disable the holds
  // on these GPIOs.
  gpio_hold_dis(static_cast<gpio_num_t>(fwd_pin_));
  gpio_hold_dis(static_cast<gpio_num_t>(rev_pin_));
}

void ServoMotor::Update() {
  constexpr TickType_t update_freq = pdMS_TO_TICKS(2);
  TickType_t last_wake_time = xTaskGetTickCount();

  int prev_pulse = 0;
  ESP_ERROR_CHECK(pcnt_unit_get_count(this->unit_, &prev_pulse));
  uint64_t last_micros = micros();

  float prev_speed = 0;
  const float alpha = 0.1;

  Control control, new_control;
  int seq = 0;
  uint64_t last_log_micros = micros();
  while (true) {
    if (!xTaskDelayUntil(&last_wake_time, update_freq)) {
      log_d("missed deadline");
    }
    portENTER_CRITICAL(&control_mutex_);
    new_control = control_;
    portEXIT_CRITICAL(&control_mutex_);

    if (control.mode != new_control.mode) {
      pid_.Reset();
    }
    control = new_control;
    
    int cur_pulse = 0;
    ESP_ERROR_CHECK(pcnt_unit_get_count(this->unit_, &cur_pulse));
    uint64_t current_micros = micros();
    int dpulse = cur_pulse - prev_pulse;
    uint64_t delta_micros = current_micros - last_micros;
    const float pulse_per_output_rev = 7 * 4 * 30;
    
    const float pps = (1.0 * dpulse / delta_micros) * 1000000;
    const float rps = pps / pulse_per_output_rev;
    const float dps = rps * 360;

    float new_speed = alpha * dps + (1 - alpha) * prev_speed;
    portENTER_CRITICAL(&control_mutex_);
    speed_ = new_speed;
    portEXIT_CRITICAL(&control_mutex_);

    int output_duty;

    if (control.mode == ControlMode::kSpeed) {
      float dt = static_cast<float>(delta_micros) / 1000000.0f;
      float output = pid_.Compute(control.setpoint, new_speed, dt);
      output_duty = static_cast<int>(output);
      OutputDuty(output_duty);
    } else  {
      output_duty = control.setpoint;
      OutputDuty(output_duty);
    }

#if 0
    if (current_micros - last_log_micros > 20000) {
      last_log_micros = current_micros;
      uint32_t timestamp = current_micros / 1000;
      printf(">setpoint:%d:%d\n", timestamp, control.setpoint);
      printf(">state:%d:%f\n", timestamp, new_speed);
      printf(">output:%d:%d\n", timestamp, output_duty);
      printf(">i:%d:%f\n", timestamp, pid_.i());  
      printf(">p:%d:%f\n", timestamp, pid_.p());
      printf(">d:%d:%f\n", timestamp, pid_.d());
      printf(">err:%d:%f\n", timestamp, pid_.error());
    }
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

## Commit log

2026-01-26 Various updates, kicad schematic
    [sbrb.kicad_pcb, sbrb.kicad_sch]
2026-01-27 Initial schematic
    [sbrb.kicad_pcb, sbrb.kicad_sch]
2026-01-27 Finishe design
    [sbrb.kicad_pcb, sbrb.kicad_sch]
2026-01-29 Add diode to schematic.
2026-01-30 Add needed diode.
    [sbrb.kicad_sch]
2026-01-31 Reduce frequency of steering control.
2026-02-02 Complete rework for ESP-IDF.
    [ServoMotor.cpp, main.cpp]
2026-02-04 Revise BOM with additional components and clarifications
    Updated parts list with additional details and corrections.
